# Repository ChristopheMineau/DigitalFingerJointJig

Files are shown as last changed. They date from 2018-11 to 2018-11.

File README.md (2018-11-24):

# DigitalFingerJointJig
Arduino code and other files for my Digital Finger Joint Jig woodworking machine.  

# What it is all about
This project is both a hardware and Software project.  
It is related to woodworking tooling.  
The final goal is to accurately make finger joints of any width, with any blade width.  
(If this sounds weird to your ears so far ... you're free to pass your way ...)  

The project is fully described on this post on the tooling encyclopaedia homemadetools.net :  
http://www.homemadetools.net/forum/new-kind-digital-finger-joint-jig-63733#post99890

# About Me
This is personnal work from Christophe Mineau, I am an amateur craftsman and maker.  
I am in the mean time a professional software designer.  
Most of my craft work is published on my Website : www.labellenote.fr  
Most of my tooling work is also published on HomeMadeTools.net : http://www.homemadetools.net/builder/Christophe+Mineau   

# License
This work can be shared under the respect of the Creative Commons License: CC BY-NC-SA 4.0  
  

# Components
Everything is home build, using the following purchased components :  
## Arduino board :
Nano V3 is just fine and tiny  
## IR sensors
These are FC-51 IR sensors, same as described here :  
http://gilles.thebault.free.fr/spip.php?article37  
I have un-soldered the LEDS and made a black plastic mount for my rotary encoder, in order to get them at the right spacing.  
I re-connected the mounted leds to the sensor via short wires.  

These happened to be quite difficult to use eventually, generating a lot of bouncing.  
My first version using interrupts was practically un-usable, and I had to code this final version using a polling technique 
and a strong anti-bouncing algorythm.  
I am thinking now that I should have gone the magnetic/hall effect sensor way ...  

# Known issues
In the shop environment (proximity of the table saw motor), I have from time to time some erratic behaviors,
thought this is quite rare.  

# TODO
Redo the rotary sensor using hall effect sensors.  

# ReUse
Feel free to re-use and send me a feed back in case of success :)

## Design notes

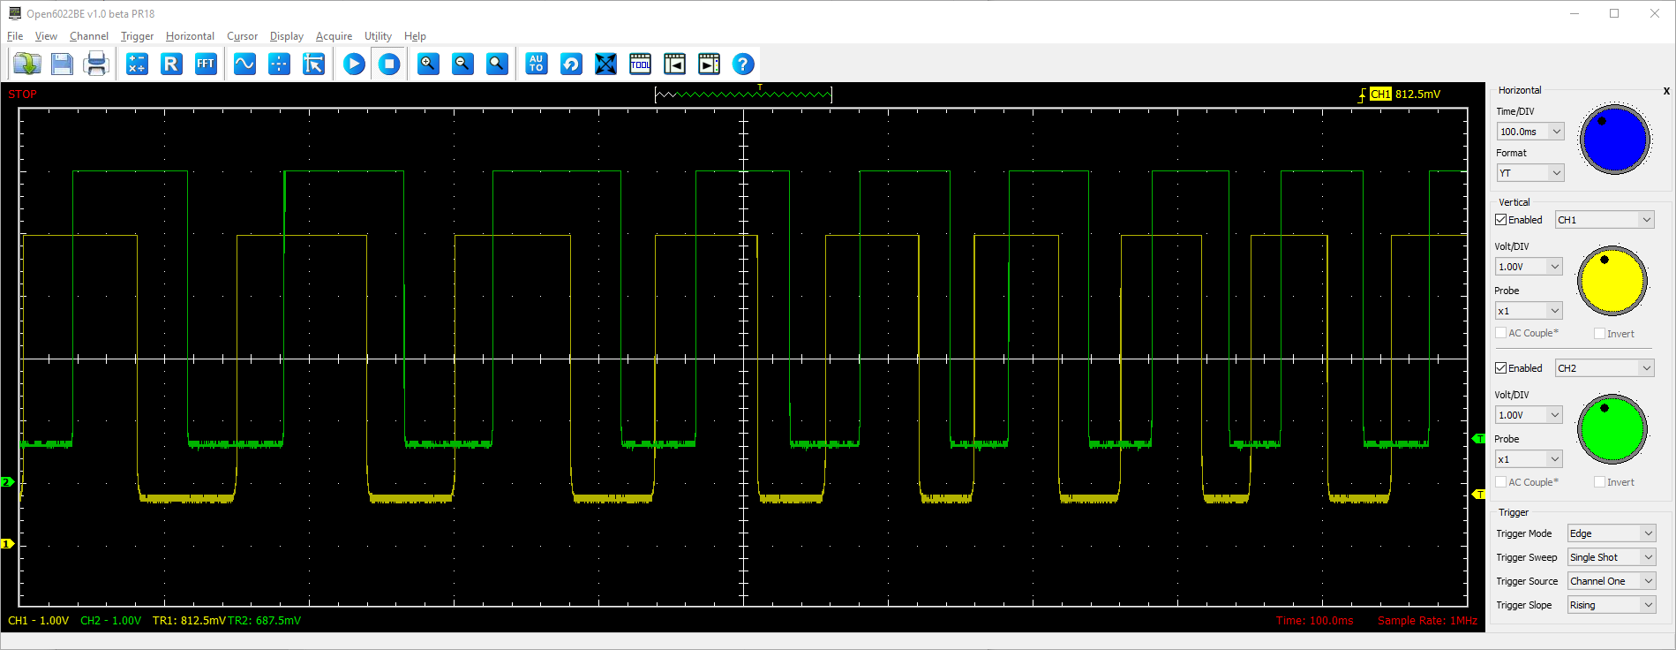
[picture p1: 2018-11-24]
anticlockwise.png

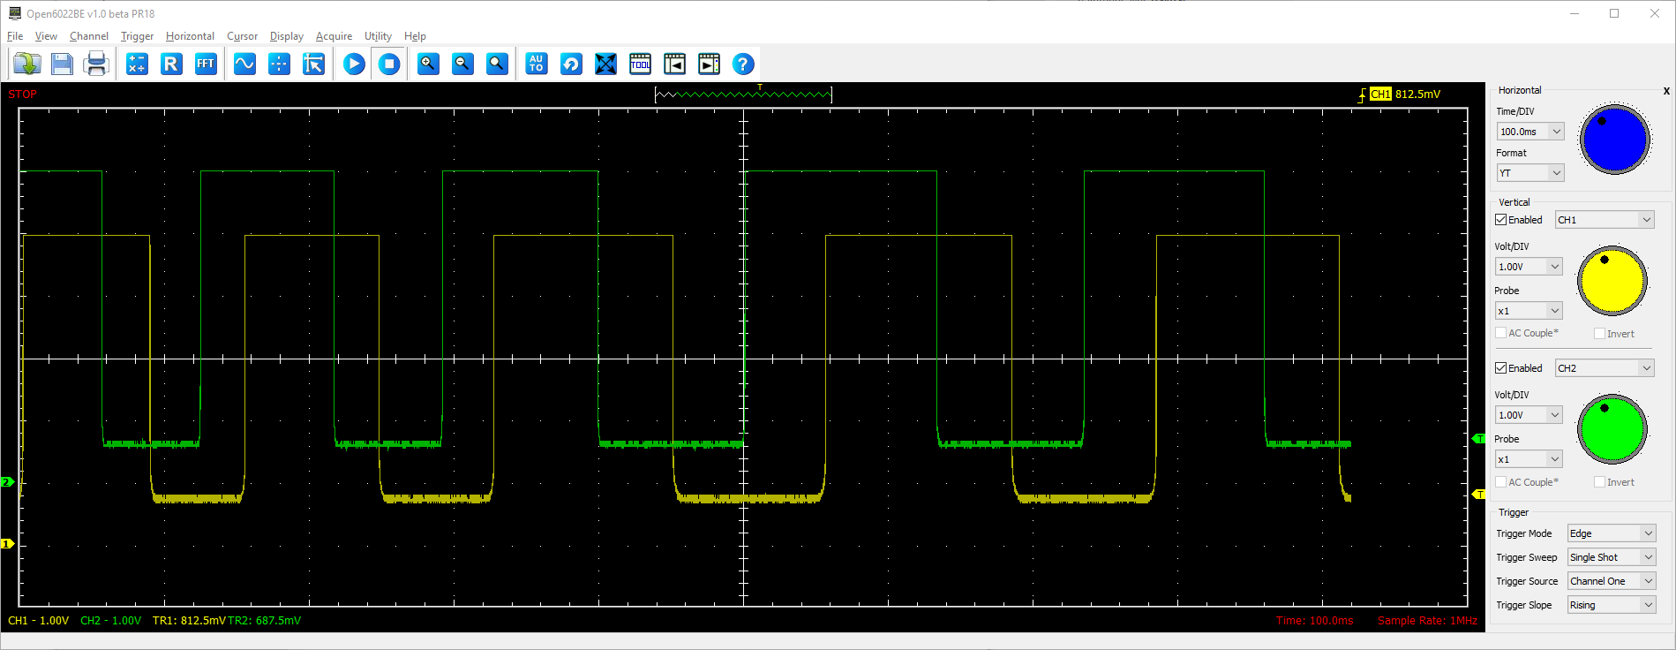
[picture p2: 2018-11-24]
cloclwise.png

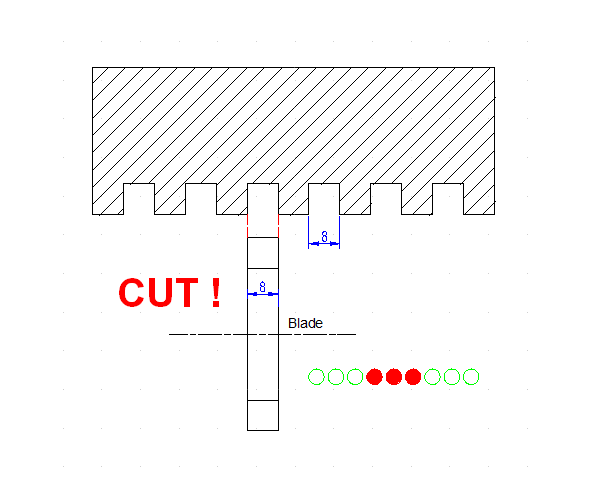
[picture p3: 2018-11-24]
Animation_8mm.gif

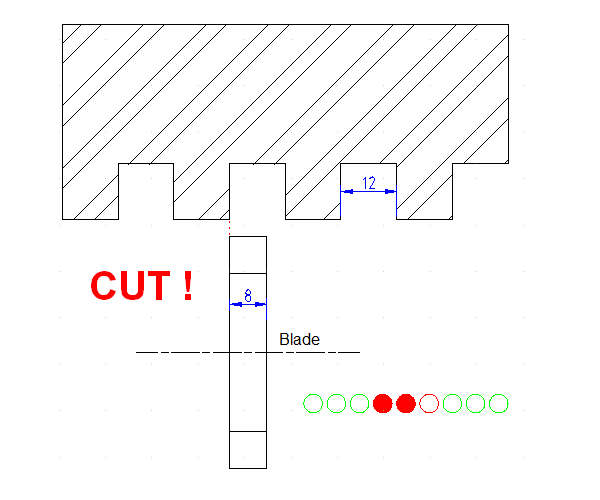
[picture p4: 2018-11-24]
Animation_12mm.gif

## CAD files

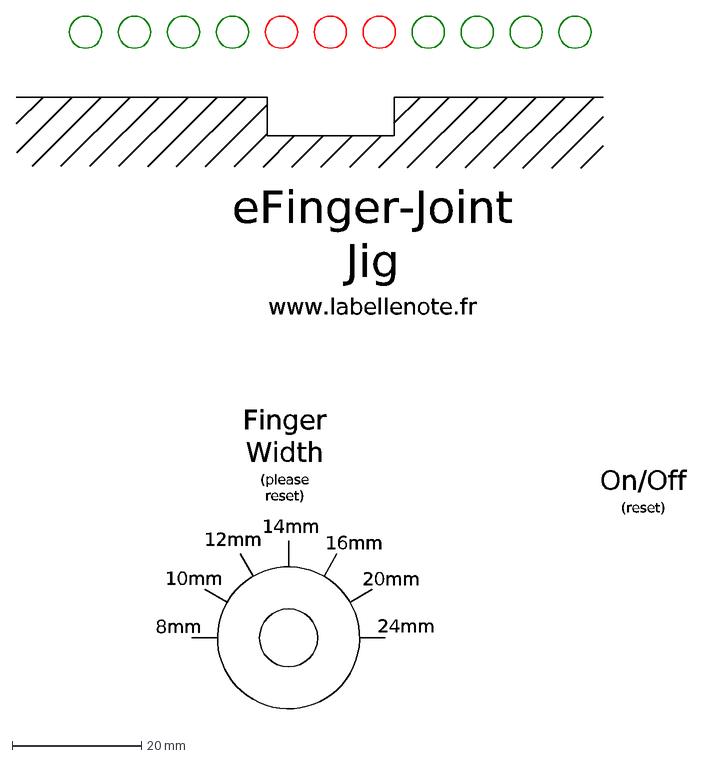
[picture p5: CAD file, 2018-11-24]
eFingerJointJig_FrontPlate.dxf
10mm
12mm
14mm
16mm
20mm
24mm
8mm
Finger Width (please reset)
On/Off (reset)
eFinger-Joint Jig www.labellenote.fr

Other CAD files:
Config lame.dxf

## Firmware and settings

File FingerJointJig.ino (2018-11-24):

/* Arduino Code for the digital FingerJoint Jig, by C.Mineau, 2017 may 1st, www.labellenote.fr
 *  
 *  setup : 2 IR LED modules are used and mounted as a quadature encoder on a wheel drilled with equidistant holes  
 *  If distance between 2 holes = 2*PI, the 2 leds are spaced by 2*PI/4 (+n*2PI) 
 *  In my case : 1 screw turn = 54 sectors with 27 holes , spaced by 4 mm . Leds spaced by 10mm
 *  
 *  1 screw turn = carriage moves by 1 screw pych value.
 *  In my case screw= M10, pitch= 1.5 mm
 *  
 *  Led A (right hand looking at the end of the screw) connected to Pin 3
 *  Led B (left hand looking at the end of the screw) connected to Pin 2
 *  
 *  Positive values of displacements correspond to right motion of the carriage (clockwise motion of the crank)
 */

#include <math.h>

#define VERSION "digital Finger Joint Jig by C.Mineau - version 3.0"
#define SCREW_PITCH 1.5   // mm
#define BLADE_WIDTH 8  // mm
#define STEP_PER_TURN 27
#define LED_A 3   // right
#define LED_A_MASK B00001000
#define LED_B 2   // left
#define LED_B_MASK B00000100
#define ROTARY_POWER 13
#define ROTARY_READ A1
#define DEBUG_PIN A0
#define DEBUG_BUTTON_PIN A4
#define DEBUG_PIN_MASK B00000001  // on  PORTC
#define LEFT -1
#define RIGHT 1
#define UP 1
#define DOWN 0
#define DEBOUNCING_TIME 600UL //Debouncing Time in microseconds
#define DEBUG_NO
#define TRACE_NO

// CLASSES Definition
struct S_bouncedInput {
  byte pinMask;   // pin number limited to 0<7 to keep on PORTD
  byte state;     // current state ;
                  // 0 = UP stable
                  // 1 = UP but DOWN change in confirmation
                  // 2 = DOWN stable
                  // 3 = DOWN but UP change in confirmation
  unsigned long lastConfirmationTime;  // in microseconds
  unsigned long pollCount;   
  unsigned long stableStateChangeCount;
  char id;
  
  S_bouncedInput (int inputPin,char id) : // constructor
    pinMask(1 << inputPin),
    
    pollCount(0),
    stableStateChangeCount(0),
    lastConfirmationTime(micros()),
    id(id)
    {
      PIND & pinMask ? state=0 : state=2;   // stable UP or DOWN upon the pin level read at init
    }
    
  byte stableState() {
    if (state >= 2) return DOWN; else return UP;
  }
  
  bool poll() {    // polls and integrate the states. Return true if rising edge on the stable state
    
    byte   pinTransientState =  PIND & pinMask;
    unsigned long currentTime =  micros();

    bool result=false;
  
    switch (state) {  
      case 0:      // 0 = UP stable 
        if (pinTransientState) 
          lastConfirmationTime=currentTime;  // No change, update confirmation time
        else
          state=1;                        // attempt to go to DOWN state, to be confirmed  
        break; 
            
      case 1:     // 1 = UP but DOWN change in confirmation
         if (pinTransientState) { 
           state=0;         // DOWN Not confirmed, coming back to stable UP
           lastConfirmationTime=currentTime;
         }  else {
           if ((currentTime-lastConfirmationTime)>=DEBOUNCING_TIME) {        //  DOWN confirmed, moving to stable DOWN 
             state=2;
             lastConfirmationTime=currentTime;
             stableStateChangeCount++;
           }
         }  
         break;
               
      case 2:     // 2 = DOWN stable
        if (pinTransientState) 
          state=3;       // attempt to go to UP state, to be confirmed      
        else
          lastConfirmationTime=currentTime;  // No change, update confirmation time                    
        break;
         
     case 3:      // 3 = DOWN but UP change in confirmation 
        if (pinTransientState) {
          if ((currentTime-lastConfirmationTime)>=DEBOUNCING_TIME) {    //  UP confirmed, moving to stable UP 
            state=0;
            lastConfirmationTime=currentTime;
            stableStateChangeCount++;
            result=true;     // rising edge
          }
        } else {
          state=2;    // UP Not confirmed, coming back to stable DOWN
          lastConfirmationTime=currentTime;
        } 
        break;   
    }
#ifdef DEBUG    
    debug(currentTime,pinTransientState,result);
#endif    
    pollCount++;
    return result;

  }

  void debug(unsigned long t, byte ts,bool r) {
      Serial.print(" time=");
      Serial.print(t);
      Serial.print(" id=");
      Serial.print(id);
      Serial.print(" pinTransientState=");
      Serial.print(ts);
      Serial.print(" result=");
      Serial.print(r);
      Serial.print(" state=");
      Serial.print(state);
      Serial.print(" stableStateChangeCount=");
      Serial.print(stableStateChangeCount);
      Serial.println("");    
  }
};

struct LedBarGraph {
/*  LED Bargraph to display the carriage position on the eFingerJoint Jig
4 green Leds on the LEFT for the half finger on the left of a cut
3 red Leds in the middle for the cut indication
  - in case fingerWidth=bladeWidth : the three LEDS are lit up
  - in case the blade is narrower than the finger, led of Left means the blade is set for the Left edge of the cut
  and the right led is lit if the blade is set to cut the right edga of the cut.
  In case the finger is wider more than 2 times the width of the blade, the middle LED is lit in intermediate position. 

  * Constructor must be called giving the blade and finger width parameters
  * update method with a position parameter can be called in order to display this position on the bargraph
  * Position 0 correspond to the first cut, right edge of the cut.     

*/


  int  pinNumber[11] = { 4, 5, 6, 7, 8, 9, 10,11,12,16,17} ;  //  note:    A0 = 14 < A7=21
  //                     G  G  G  G  R  R  R  G  G  G  G        from right to left   
  //                     0  1  2  3  4  5  6   7  8  9 10
  //                     right                       left
  
  int greenLedIdx[8] = {7,8,9,10,0,1,2,3} ; //  order of green Leds to be lit according to distance to be moved

// all units expressed in steps in order to avoid any floating point calculation in runtime
  int bladeWidth;     // In Steps, can not be bigger than finger width
  int fingerWidth;    // In Steps, can be bigger than blade width
  long previousPosition;  // in Steps
  float greenStep;      // in steps
  
  void init(int bldeWidth, int fgerWidth){    // to be called in setup 
    bladeWidth=bldeWidth;
    fingerWidth=fgerWidth;
    greenStep = (float(fingerWidth+bladeWidth)/8); 
    for(int i=0;i<11;i++) {      
        pinMode(pinNumber[i], OUTPUT);
        digitalWrite(pinNumber[i],LOW);
    } 
    setRedLeds(0);    // The blade is supposed to be aligned with position 0 at initialization
  }
    
  void update(long position) {   //      to be called with a new position (in steps)
    
    if (position==previousPosition) {
      return;   // save time
    }
    int finger=floor(double(position)/(2*fingerWidth));         // number of full finger   (full finger = 1 cut + 1 finger)
    int offset= position-finger*2*fingerWidth;    // offset within the full finger 
    setRedLeds(offset);
    setGreenLeds(offset);
    previousPosition=position;
  }
    
  void setRedLeds(int offset) {    // offset is the displacement within the current finger cut
     approxR(offset,0) ? digitalWrite(pinNumber[4],HIGH):digitalWrite(pinNumber[4],LOW);    // right cut edge Led
     approxL(offset,fingerWidth-bladeWidth) ? digitalWrite(pinNumber[6],HIGH):digitalWrite(pinNumber[6],LOW);    // left cut edge Led
     offset <=fingerWidth-bladeWidth ? digitalWrite(pinNumber[5],HIGH):digitalWrite(pinNumber[5],LOW);    // middle cut Led
  }
   
  void setGreenLeds(int offset) {
        int g0 =fingerWidth-bladeWidth;  
        for (int i = 0; i<8; i++) {
          approx2(offset, g0+ i*greenStep) ? digitalWrite(pinNumber[greenLedIdx[i]],HIGH):digitalWrite(pinNumber[greenLedIdx[i]],LOW);  
        }        

  } 
  
  bool approxR(int p1, int p2) {   // checks if two positions are close enough (right edge)
    return  ((p1>=p2) && (p1-p2)<1) ?  true :  false;
  }  
  bool approxL(int p1, int p2) {   // checks if two positions are close enough  (left edge)
    return  ((p2>=p1) && (p2-p1)<1) ?  true :  false;
  }
  bool approx2(int p1, int p2) {   // checks if two positions are close enough
    return  ((p1>p2) && (p1-p2)<=greenStep) ?  true :  false;
  }

  void debug() {
    static bool alreadyPrint = false;
    if (!alreadyPrint) {   
      Serial.print(" bladeWidth=");
      Serial.print(bladeWidth);
      Serial.print(" fingerWidth=");
      Serial.print(fingerWidth);
      Serial.print(" greenStep=");
      Serial.print(greenStep);
      Serial.println("");  
    }
      alreadyPrint=true;
  }
    
}  ;

struct S_RotarySelector {
  int powerPin;  // to avoid consuming too much power, the Rotary is powered only during polling
  int readPin;

  void init(int pwerPin, int rdPin) {   // to be called in setup
    powerPin=pwerPin;
    readPin=rdPin;
    pinMode( powerPin, OUTPUT);
  }

  int poll() {
    digitalWrite(powerPin,HIGH);
    delay(100);
    int val=analogRead(readPin);
    digitalWrite(powerPin,LOW);

    if (val>=0 && val<85) return 8;
    if (val>86 && val<255) return 10; 
    if (val>256 && val<425) return 12;
    if (val>426 && val<595) return 14;    
    if (val>596 && val<765) return 16;
    if (val>766 && val<935) return 20;    
    if (val>936) return 24;
  }

  void debug() {  // never ends
    Serial.print(" S_RotarySelector.powerPin=");
    Serial.print(powerPin);
    Serial.print(" S_RotarySelector.readPin=");
    Serial.println(readPin);
    while (1) {
        digitalWrite(powerPin,HIGH); 
        int val=analogRead(readPin);
        Serial.print(" analogRead=");
        Serial.print(val); 
        Serial.print(" poll()=");
        Serial.println(poll());
       delay(1000);
    }
    digitalWrite(powerPin,LOW);
  }
  
} ;

// GLOBALS :

// GLobal variables
long  Steps = 0;   // keeps the current step position in steps
int fingerWidth=0;
long previousSteps = 0;
int  Direction = 0;        // current Direction = LEFT or RIGHT
float  Position = 0;       // Current Position in mm 
float stepRatio = SCREW_PITCH / STEP_PER_TURN;   // mm / step
int Finger = 0;            // current finger number 
unsigned long risingEdgeCount=0;


// Global objects
// Rotary Encoder led objects :
S_bouncedInput ledA(LED_A,'A');
S_bouncedInput ledB(LED_B,'B');
// Rotary selector
S_RotarySelector rotarySelector;
// Display bargraph object :
LedBarGraph bargraph;



void setup() {
  Serial.begin (19200);
  Serial.println("--------------------------------------------------");
  Serial.println(VERSION);
  Serial.println("--------------------------------------------------");
  

  pinMode(LED_A, INPUT);
  pinMode(LED_B, INPUT);
  pinMode(DEBUG_BUTTON_PIN, INPUT_PULLUP);   // for debug, wire a button to trigger traces on serial link
  pinMode(DEBUG_PIN, OUTPUT);   // for debug : changes state at each step
  
  rotarySelector.init(ROTARY_POWER, ROTARY_READ);
  fingerWidth=rotarySelector.poll(); 
  bargraph.init(int(BLADE_WIDTH/stepRatio) , int(fingerWidth/stepRatio));

  Serial.print(" BladeWidth=");
  Serial.print(BLADE_WIDTH);
  Serial.print(" FingerWidth=");
  Serial.println(fingerWidth);
  
//  bargraph.debug();
//  rotarySelector.debug();
}

void loop() {
  // Polling
  ledB.poll();
  if (ledA.poll()) {    // If rising edge on Led A 
    ledB.stableState()  ?  Direction=LEFT : Direction=RIGHT;   // Have a look at led B level to know the direction
    PORTC ^= DEBUG_PIN_MASK ;   // For debug purpose, reverts DEBUG_PIN at each step (use a probe on that pin to check if lost steps, compared to LEDA)
    Steps += Direction;
    risingEdgeCount++;
    bargraph.update(Steps);
  }

    
  if (digitalRead(DEBUG_BUTTON_PIN)==LOW) {                        // if trace button wired on A4
    int finger=floor(double(Steps)/(2*180));         // number of full finger   (full finger = 1 cut + 1 finger)  here 180=fingerWidth=10mm
    int offset= Steps-finger*2*180;  
    Serial.print(" Steps=");
    Serial.print(Steps);
    Serial.print(" finger=");
    Serial.print(finger);
    Serial.print(" offset=");
    Serial.print(offset);
    Serial.println("");
  }

#ifdef TRACE
  Position=Steps*stepRatio;
  Finger= int(Position/(2*BLADE_WIDTH));
  Display();
  previousSteps=Steps;
#endif
}




void Display() {
  static long display_delay ;

  display_delay+=1;

#ifdef DEBUG
  if (display_delay==1000) {
    Serial.print(" ledA.state=");
    Serial.print(ledA.state);
    Serial.print(" ledA.stableStateChangeCount=");
    Serial.print(ledA.stableStateChangeCount);
    Serial.print(" ledB.state=");
    Serial.print(ledB.state);
    Serial.print(" ledB.stableStateChangeCount=");
    Serial.print(ledB.stableStateChangeCount);
    Serial.println("");
  }
#endif

  if (previousSteps!=Steps) {
    Serial.print(" risingEdgeCount=");
    Serial.print(risingEdgeCount);
    Serial.print(" Steps=");
    Serial.print(Steps);
    Serial.print(" Direction=");
    Serial.print(Direction);
    Serial.print(" Position=");
    Serial.print(Position);
    Serial.print(" Finger=");
    Serial.print(Finger);
    Serial.println("");
    display_delay=0;
  }

  if (display_delay==1000) {
    display_delay=0;
  }
   
}
